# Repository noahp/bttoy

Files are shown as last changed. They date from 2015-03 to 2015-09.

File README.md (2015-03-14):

bttoy
=====
Bluetooth robot toy.

Parts
=====
1A/40V schottky  
http://www.mouser.com/ProductDetail/AVX/SD1206T040S1R0/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

47uF electrolytic, 5x5.2mm  
http://www.mouser.com/ProductDetail/Lelon/VE-470M1CTR-0505/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

inductor  
http://www.mouser.com/ProductDetail/Bourns/SRN4012T-100M/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

switch  
http://www.mouser.com/ProductDetail/Apem/MHSS1105/?qs=sGAEpiMZZMtHXLepoqNyVYxFoZ6bbHER8MOeX4eGSrE%3d

motor ic  
http://www.mouser.com/ProductDetail/ON-Semiconductor/LV8548MC-AH/?qs=sGAEpiMZZMuleuVm2ofeX1ZeyMQNcmgu

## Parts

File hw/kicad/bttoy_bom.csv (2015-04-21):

Value | Ref | Footprint
MKL05Z32VLC4 | U4 | kicadlib:SMD_LQFP-32
MCP73831 | U3 | kicadlib:SMD_SOT23-5
USB-micro-b | J1 | kicadlib:usb_micro_b_smt
AAT3221/MIC5504 | U1 | kicadlib:SMD_SOT23-5
1K | R3 | kicadlib:SMD_0603_R
4.7uF | C6 | kicadlib:SMD_0603_R
LED | D2 | kicadlib:SMD_0603_LED
2K | R4 | kicadlib:SMD_0603_R
4.7uF | C7 | kicadlib:SMD_0603_R
1uF | C1 | kicadlib:SMD_0603_R
1uF | C4 | kicadlib:SMD_0603_R
ARM_10PIN | J3 | kicadlib:ARM_10_PIN_SMT
HC-07_BLUETOOTH | J2 | kicadlib:HC-07_bluetooth
MIC2288 | U2 | kicadlib:SMD_SOT23-5
10uH/650mA (LQH43CN100K03) | L1 | kicadlib:SMD_4x4_INDUCTOR
2.2uF/10V | C5 | kicadlib:SMD_0603_R
10uF/16V | C3 | kicadlib:SMD_0805_R
40v/1A | D1 | kicadlib:SMD_1206_DIODE
6.2K | R1 | kicadlib:SMD_0603_R
1K | R2 | kicadlib:SMD_0603_R
MPS ENABLE | JP1 | kicadlib:jmp_small
SPDT (Apem MHSS1105) | SW1 | kicadlib:TH_APEM_MHSS1105_SPDT
30uF | C2 | kicadlib:SMD_5X5.2_CAP
LV8548 | U5 | kicadlib:SMD_SOIC-10NB
M1+ | P10 | kicadlib:TEST_0.100
M1- | P11 | kicadlib:TEST_0.100
M2+ | P12 | kicadlib:TEST_0.100
M2- | P13 | kicadlib:TEST_0.100
+9V_DBG | P1 | kicadlib:TEST_0.100
LED | D3 | kicadlib:SMD_0603_LED
1K | R5 | kicadlib:SMD_0603_R
LED | D4 | kicadlib:SMD_0603_LED
1K | R6 | kicadlib:SMD_0603_R
LED | D5 | kicadlib:SMD_0603_LED
1K | R7 | kicadlib:SMD_0603_R
spi_mosi | P6 | kicadlib:TEST_0.100
spi_miso | P5 | kicadlib:TEST_0.100
spi_ss | P4 | kicadlib:TEST_0.100
spi_clk | P7 | kicadlib:TEST_0.100
i2c_sda | P2 | kicadlib:TEST_0.100
i2c_scl | P3 | kicadlib:TEST_0.100
+3.3v | P8 | kicadlib:TEST_0.100
gnd | P9 | kicadlib:TEST_0.100
B- | P14 | kicadlib:TEST_0.100
B+ | P15 | kicadlib:TEST_0.100

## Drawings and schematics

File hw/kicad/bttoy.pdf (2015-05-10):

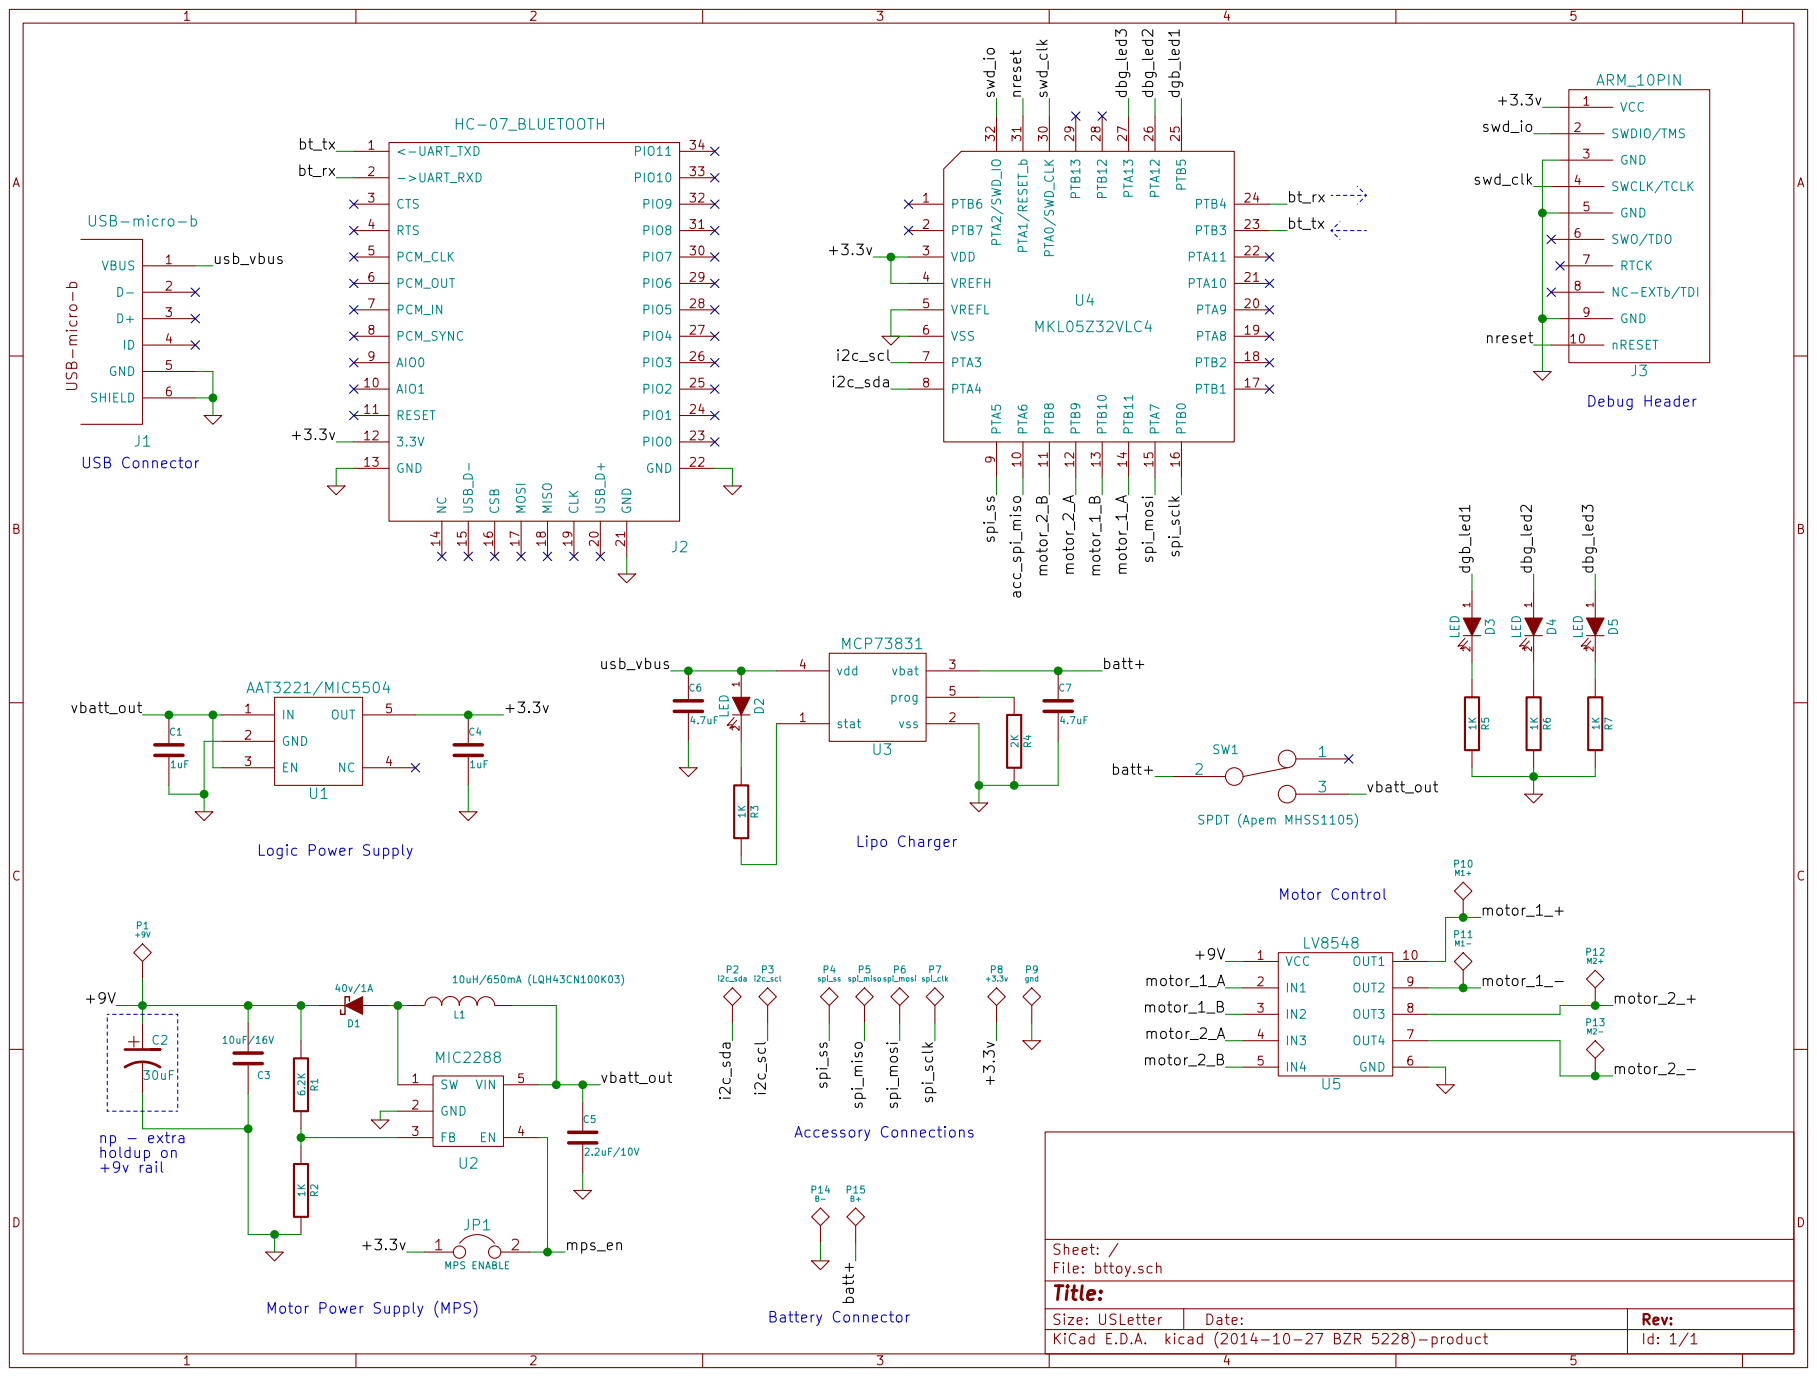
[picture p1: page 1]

Lipo Charger Logic Power Supply

File: bttoy.sch Sheet: /

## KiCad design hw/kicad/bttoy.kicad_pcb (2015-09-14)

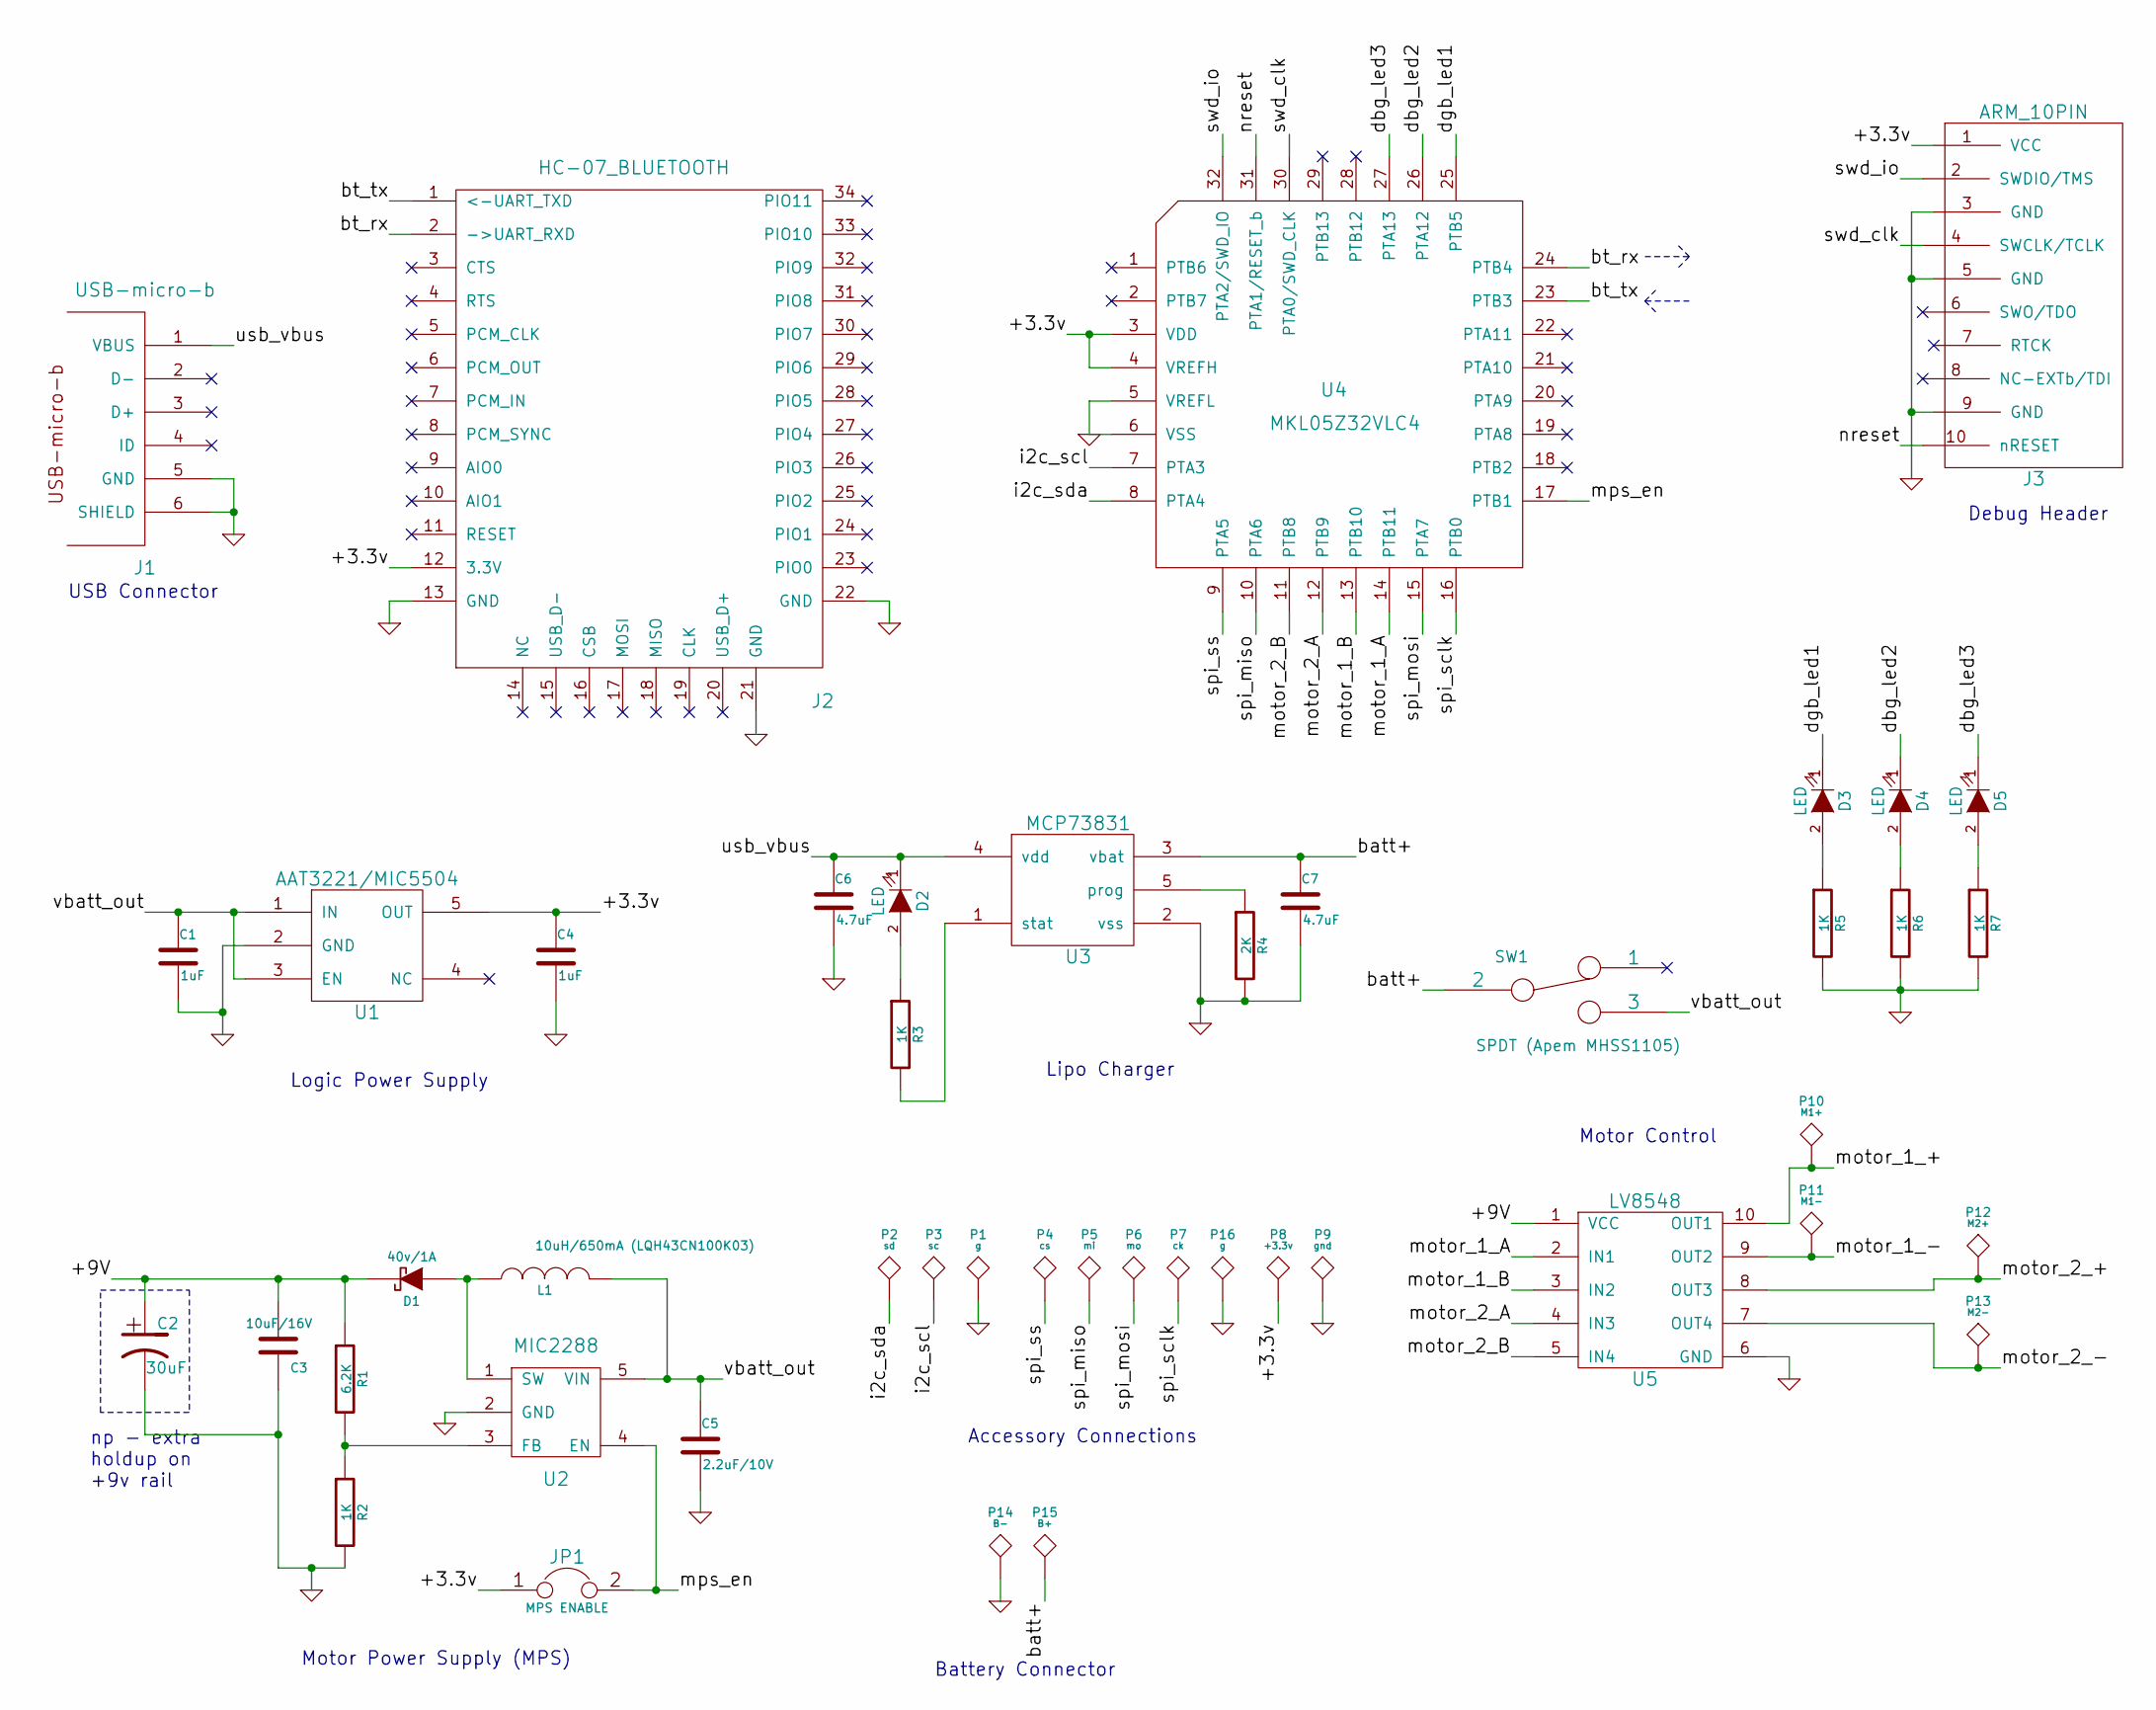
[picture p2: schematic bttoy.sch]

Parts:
C1, C4: 1uF; SMD_0603_R
C2: 30uF; SMD_5X5.2_CAP
C3: 10uF/16V; SMD_0805_R
C5: 2.2uF/10V; SMD_0603_R
C6, C7: 4.7uF; SMD_0603_R
D1: 40v/1A; SMD_1206_DIODE
D2, D3, D4, D5: LED; SMD_0603_LED
J1: USB-micro-b; usb_micro_b_smt
J2: HC-07_BLUETOOTH; HC-07_bluetooth
J3: ARM_10PIN; ARM_10_PIN_SMT
JP1: MPS ENABLE; jmp_small
L1: 10uH/650mA (LQH43CN100K03); SMD_4x4_INDUCTOR
P1, P16: g; TEST_0.100
P2: sd; TEST_0.100
P3: sc; TEST_0.100
P4: cs; TEST_0.100
P5: mi; TEST_0.100
P6: mo; TEST_0.100
P7: ck; TEST_0.100
P8: +3.3v; TEST_0.100
P9: gnd; TEST_0.100
P10: M1+; TEST_0.100
P11: M1-; TEST_0.100
P12: M2+; TEST_0.100
P13: M2-; TEST_0.100
P14: B-; TEST_0.100
P15: B+; TEST_0.100
R1: 6.2K; SMD_0603_R
R2, R3, R5, R6, R7: 1K; SMD_0603_R
R4: 2K; SMD_0603_R
SW1: SPDT (Apem MHSS1105); TH_APEM_MHSS1105_SPDT
U1: AAT3221/MIC5504; SMD_SOT23-5
U2: MIC2288; SMD_SOT23-5
U3: MCP73831; SMD_SOT23-5
U4: MKL05Z32VLC4; SMD_LQFP-32
U5: LV8548; SMD_SOIC-10NB

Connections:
/+3.3v: C4.1, J2.12 (3.3V), J3.1 (VCC), JP1.1, P8.1, U1.5 (OUT), U4.3 (VDD), U4.4 (VREFH)
/+9V: C2.1, C3.1, D1.2 (K), R1.1, U5.1 (VCC)
/batt+: C7.1, P15.1, SW1.2, U3.3 (vbat)
/bt_rx: J2.2 (->UART_RXD), U4.24 (PTB4)
/bt_tx: J2.1 (<-UART_TXD), U4.23 (PTB3)
/dbg_led2: D4.1 (K), U4.26 (PTA12)
/dbg_led3: D5.1 (K), U4.27 (PTA13)
/dgb_led1: D3.1 (K), U4.25 (PTB5)
/i2c_scl: P3.1, U4.7 (PTA3)
/i2c_sda: P2.1, U4.8 (PTA4)
/motor_1_+: P10.1, U5.10 (OUT1)
/motor_1_-: P11.1, U5.9 (OUT2)
/motor_1_A: U4.14 (PTB11), U5.2 (IN1)
/motor_1_B: U4.13 (PTB10), U5.3 (IN2)
/motor_2_+: P12.1, U5.8 (OUT3)
/motor_2_-: P13.1, U5.7 (OUT4)
/motor_2_A: U4.12 (PTB9), U5.4 (IN3)
/motor_2_B: U4.11 (PTB8), U5.5 (IN4)
/mps_en: JP1.2, U2.4 (EN), U4.17 (PTB1)
/nreset: J3.10 (nRESET), U4.31 (PTA1/RESET_b)
/spi_miso: P5.1, U4.10 (PTA6)
/spi_mosi: P6.1, U4.15 (PTA7)
/spi_sclk: P7.1, U4.16 (PTB0)
/spi_ss: P4.1, U4.9 (PTA5)
/swd_clk: J3.4 (SWCLK/TCLK), U4.30 (PTA0/SWD_CLK)
/swd_io: J3.2 (SWDIO/TMS), U4.32 (PTA2/SWD_IO)
/usb_vbus: C6.1, D2.1 (K), J1.1 (VBUS), U3.4 (vdd)
/vbatt_out: C1.1, C5.1, L1.2, SW1.3, U1.1 (IN), U1.3 (EN), U2.5 (VIN)
GND: C1.2, C2.2, C3.2, C4.2, C5.2, C6.2, C7.2, J1.5 (GND), J1.6 (SHIELD), J2.13 (GND), J2.21 (GND), J2.22 (GND), J3.3 (GND), J3.5 (GND), J3.9 (GND), P1.1, P9.1, P14.1, P16.1, R2.2, R4.2, R5.2, R6.2, R7.2, U1.2 (GND), U2.2 (GND), U3.2 (vss), U4.5 (VREFL), U4.6 (VSS), U5.6 (GND)
unnamed: D1.1 (A), L1.1, U2.1 (SW)
unnamed: D2.2 (A), R3.1
unnamed: D3.2 (A), R5.1
unnamed: D4.2 (A), R6.1
unnamed: D5.2 (A), R7.1
unnamed: R1.2, R2.1, U2.3 (FB)
unnamed: R3.2, U3.1 (stat)
unnamed: R4.1, U3.5 (prog)

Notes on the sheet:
Lipo Charger
Logic Power Supply
Debug Header
USB Connector
Motor Power Supply (MPS)
np - extra holdup on +9v rail
Motor Control
Accessory Connections
Battery Connector

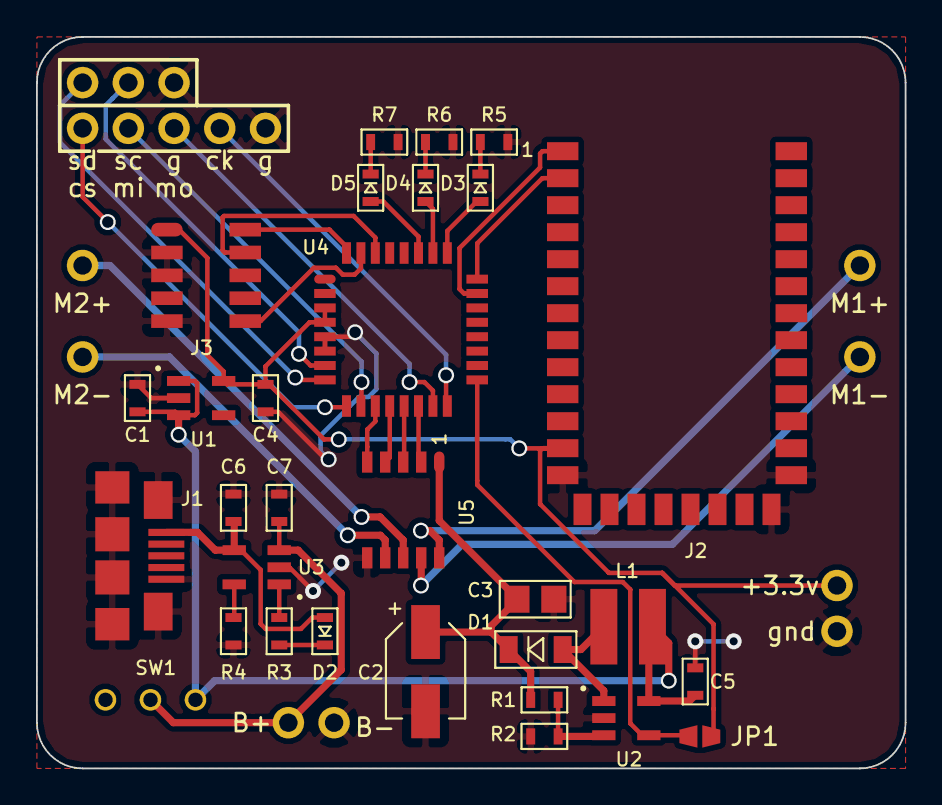
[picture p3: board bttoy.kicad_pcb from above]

Board: 2 copper layers, 48.3 x 40.6 mm, 46 parts (0 on the bottom side), 37 nets.

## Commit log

2014-11-26 - add kicad project, just schematic for now
    [bttoy.sch]
2014-11-26 - add kicadlib submodule
2014-12-02 - add libs
    [bttoy.sch]
2014-12-22 - start basic schematic, few ic's
    [bttoy.sch]
2015-02-27 - start flushing out subsystems
    [bttoy.sch]
2015-03-02 - flesh out schematic, add MPS using MIC2288 boost controller
    [bttoy.sch]
2015-03-02 - add reference part # for inductor
    [bttoy.sch]
2015-03-02 - change high side switches to pfet
    [bttoy.sch]
2015-03-08 - remove sub schematic, replace discrete motor control with LV8548 IC
    [bttoy.sch]
2015-03-08 - add motor connectors
    [bttoy.sch]
2015-03-08 - fill out motor control subsystem
    [bttoy.sch]
2015-03-14 - update to latest kicadlib
2015-03-14 - more work on schematic
    [bttoy.sch]
2015-03-14 - more schematic work
    [bttoy.sch]
2015-03-14 - start layout
    [bttoy.kicad_pcb, bttoy.sch]
2015-04-01 - new version of kicadlib with bom generator script
2015-04-01 - update to fixed hc-07 bluetooth footprint
    [bttoy.kicad_pcb]
2015-04-12 - connect motor control signals
    [bttoy.sch]
2015-04-18 - add bom, add acc. connections, reload parts on pcb
    [bttoy.kicad_pcb, bttoy.sch, bttoy_bom.csv]
2015-04-21 tune up schematic a bit more, and start positioning footprints on pcb
    [bttoy.kicad_pcb, bttoy.sch, bttoy_bom.csv]
2015-04-25 mps and dbg led's laid out
    [bttoy.kicad_pcb, bttoy.sch]
2015-05-10 arrange footprint groups in pcb, change position of power switch to control all batt output
    [bttoy.kicad_pcb, bttoy.sch]
2015-08-10 update submodule to fix lqfp-32 footprint
2015-09-14 place test points
    [bttoy.kicad_pcb, bttoy.sch]
2015-09-14 gerbers and done
    [bttoy-B_Cu.gbr, bttoy-B_Mask.gbr, bttoy-B_SilkS.gbr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]
